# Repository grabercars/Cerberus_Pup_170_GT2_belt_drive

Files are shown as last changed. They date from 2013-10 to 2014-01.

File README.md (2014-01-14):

Cerberus Pup
========

Derivative of the Rostock 3D delta printer - A big thanks goes out to all of the people who inspired this design. There are many. 

[cc by sa 3.0]

Cerberus Pup 170 GT2 belt drive
========

1/13/2014

Cerberus Pup 170 Gt2 is a 3D Delta Robot printer that uses GT2 toothed belts and 16 or 20t pulleys. Features include Magnetic Ball joint rods (Magballs), An aluminum hotend mounting bracket that is hinged and allows the hotend tip to function as the z_probe. Bowden tube direct drive easy-load spring tensioned lever arm extruder. 170mm print surface. 500mm tall with 175mm print height.

You will need to make a set of effector rods 215mm long tip-to-tip with 3/8" ball bearings bonded to the ends. Make your own or these are available from Steve Graber - grabercars@gmail.com.

Notes:

All machined parts required to build Cerberus Pup are now all available for purchase at http://3d.grabercars.com. They are manufactured on a CNC lathe to very tight tolerances.

VERTICAL CARRIAGE DRIVE SYSTEM:
Requires GT2 belts and 20T (or 16T) pulleys. Each upper gt2 belt idler consists of 2x 623 bearings placed side-by-side. 

VERTICAL CARRIAGES:
The Cerberus vertical carriages move up and down the extrusion towers by rolling on 3 cnc machined delrin 'V' rollers per carriage. Each roller consists of a cnc machined delrin cover with two 623 bearing pressed in. The roller rides in the T-Slot of the OpenBeam or Misumi 1515 extrusion. This makes for a very smooth and accurate linear carriage system. Dual 623 V Rollers can be purchased from 3d.grabercars.com - You can use either version of the roller, the Dual 623 WIDE V or the Dual 623 V.

BELT TENSION SYSTEM:
The belts are open loop and are tensioned as they are inserted into the teeth of the Vertical Carriage Bearing Bracket. 

Cerberus Pup 170 is a very quiet printer which can be made even more quiet by use of the Astrosyn NEMA 17 vibration dampers. You will need to print 3x "Lower Outer Bracket-astrosyn_damper.stl" file instead of 3x "Lower Outer Bracket.stl" file.

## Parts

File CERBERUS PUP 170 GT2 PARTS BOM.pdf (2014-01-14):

## CERBERUS PUP 170 PRINTED PARTS BOM

CHK | QTY | FILE NAME | DESCRIPTION
| 3 | Lower Outer Bracket.stl
| 3 | Upper Outer Bracket.stl
| 3 | Vertical Carriage Bearing Bracket.stl
| 3 | Base Standoff.stl
| 1 | Effector End Platform.stl
| 1 | Extruder Lever Arm.stl
| 1 | Extruder Motor Base.stl
| 2 | VIKI Hanging Clip.stl | Optional - Bolts onto VIKI
| 2 | VIKI Hanging Base.stl | Optional - Bolts onto printer

## CERBERUS PUP 170 MISC PARTS BOM

CHK | QTY | PART NAME | DESCRIPTION
| 3 | Aluminum Carriage.dxf | Vertical Carriage
| 1 | Aluminum Base Plate.dxf | Triangular plate with holes for mounting controller
| 1 | Aluminum Bottom Fan Bar.dxf | Bottom bar with holes for cooling fan
| 1 | Aluminum Bottom Button Bar.dxf | Bottom bar with hole for power button
| 1 | Aluminum Bottom Extruder Bar.dxf | Bottom bar with holes for extruder motor
| 3 | Aluminum Top Bar.dxf | Top cross bars
| 1 | Aluminum Probe Hinge Bracket - Hotend.dxf | Slotted bracket for holding hotend
| 1 | Aluminum Push-fit Bracket - Hotend.dxf | Threaded plate for push-fit connector
| 3 | Misumi 1515 Aluminum Extrusion | Vertical bar for carriage slide
| 1 | 170mm Borosilicate Disc | Printing surface
| 6 | C.F. Effector Rod | Carbon fiber arms
| 12 | 3/8” machined ball | Bonded to C.F effector rods
| 12 | 3/8 x 3/8 Cylindrical Neodymium Magnet
| 3 | 1 meter GT2 Timing Belt
| 3 | 20-tooth GT2 Pulley | Belt drive pulleys
| 6 | Pulley Grub Screw | Fastens pulley onto stepper motor
| 4 | 3mm ID round nylon spacers | Standoff spacers for mounting the controller board
| 9 | Grabercars Dual 623 V rollers
| 6 | 623ZZ bearings | Two each side by side as upper idler pulley
| 3 | P-clips – 1/4” | Wire management clips
| 1 | 1.8mm ID Teflon Tubing | Bowden tube
| 2 | Pneumatic Push-fit Insert | Bowden tube anchors
| 1 | 0.080” Steel Rod x 50mm | Bed level probe hinge

## CERBERUS PUP 170 ELECTRONIC PARTS BOM

CHK | QTY | PART NAME | DESCRIPTION
| 1 | Panucatt Azteeg X1 Control Board
| 4 | Panucatt SureStepr SD8825 Stepper Driver | 1/32nd microstepping driver
| 1 | Panucatt MC170 Hex Heated Bed | Optional heated platform
| 1 | Panucatt VIKI LCD Control Panel | Optional LCD control panel
| 1 | 203W Xbox 360 Power Supply | Printer power supply
| 1 | Xbox 360 to Xbox Slim Adaptor
| 1 | 1.75mm Hotend | Hotend, heater resistor, and thermistor
| 4 | NEMA 17 Stepper Motor
| 4 | Micro Knife Switch | Printer endstop and bed leveling probe
| 1 | 40mm Fan | Electronics Cooling
| 1 | 20mm Fan | Hotend Cooling

## CERBERUS PUP 170 FASTENERS BOM

CHK | QTY | PART | USE/DESCRIPTION
| 2 | M5x16
| 22 | M5x12
| 24 | M5 Washer
3 | M4x14
1 | M3x30
18 | M3x25
8 | M3x16
47 | M3x12
4 | M3x8
73 | M3 Washer
30 | M3 Nut
15 | M3 Nyloc
2 | M2x12
6 | M2x10
6 | M2 Washer
2 | M2 Nut

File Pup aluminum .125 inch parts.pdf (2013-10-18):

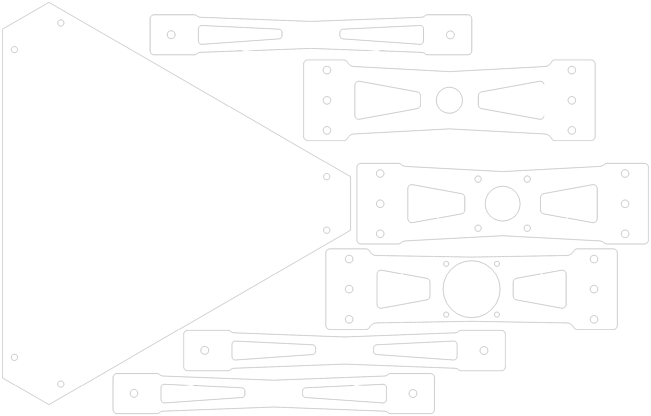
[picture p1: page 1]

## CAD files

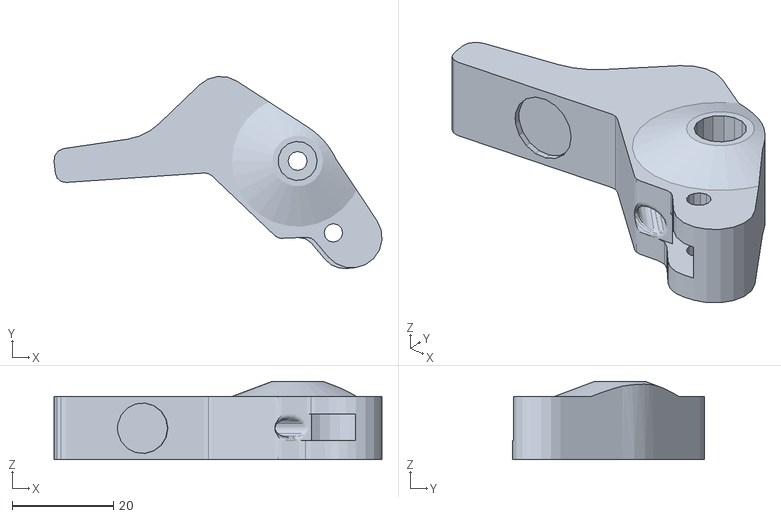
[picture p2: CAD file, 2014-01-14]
Extruder Lever Arm.stl
64.9 x 38.0 x 15.5

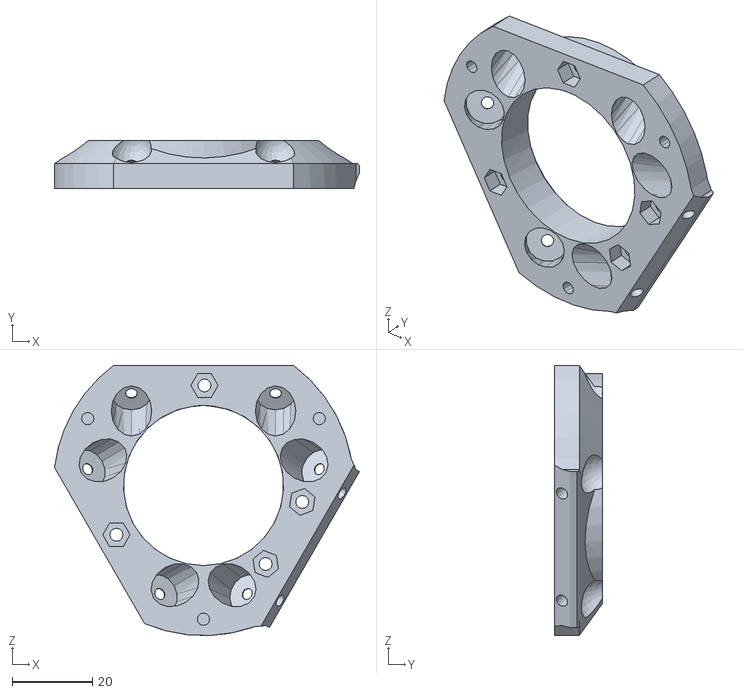
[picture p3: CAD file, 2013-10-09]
original_probe/platform_v3 - Deep Magball_original probe.stl
76.2 x 12.0 x 67.5

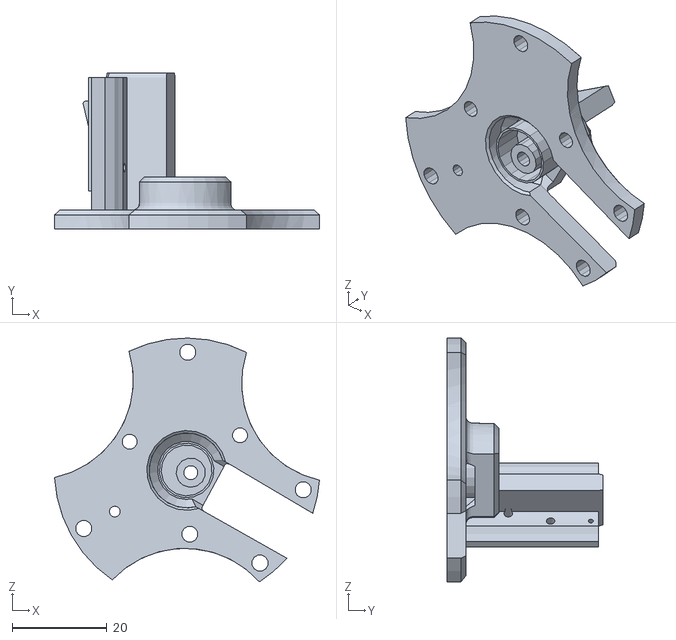
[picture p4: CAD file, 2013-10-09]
original_probe/JSlotplate_original probe.stl
56.1 x 33.1 x 51.6

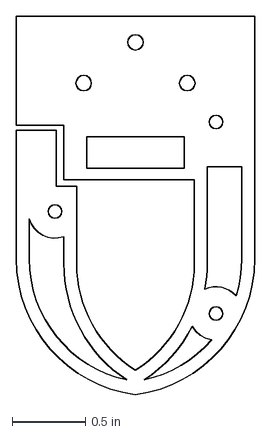
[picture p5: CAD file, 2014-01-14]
Pup vert carriage-T-6061x.125.dxf
1.63 x 2.59 in

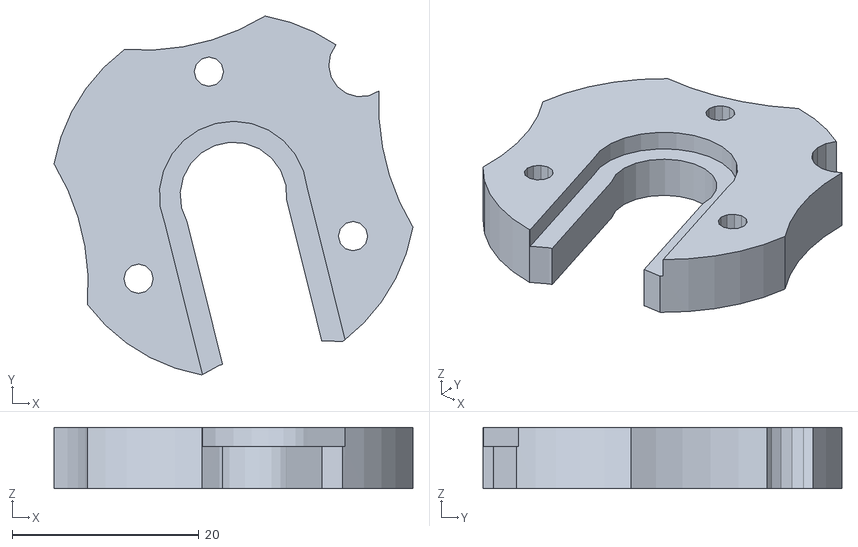
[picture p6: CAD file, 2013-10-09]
original_probe/J-slot Insert for Magball platform_original probe.stl
38.4 x 38.4 x 6.56

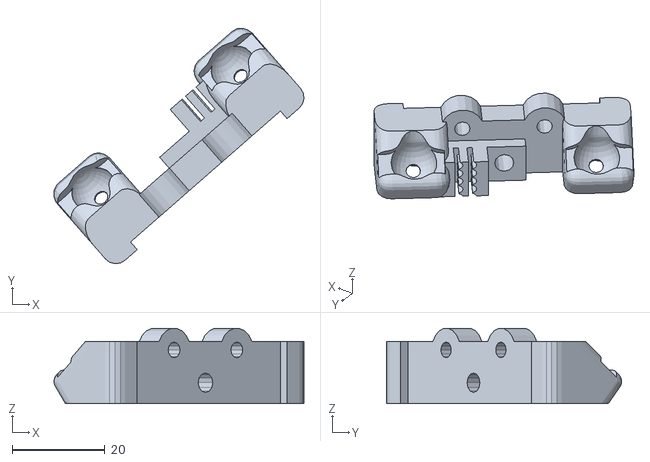
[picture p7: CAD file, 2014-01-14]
Vertical Carriage Bearing Bracket.stl
54.0 x 50.9 x 16.2

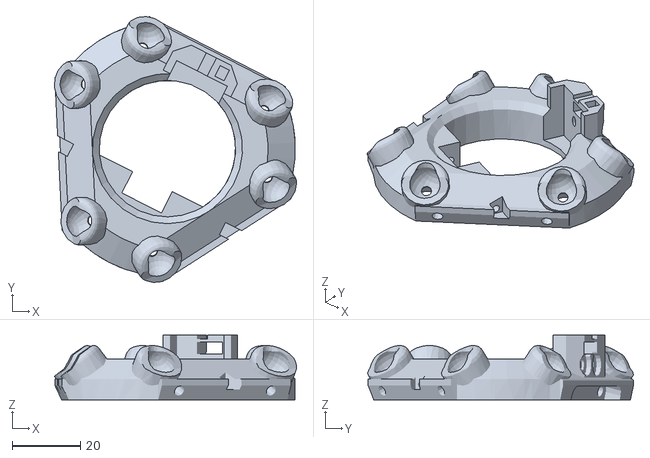
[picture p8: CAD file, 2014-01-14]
Effector End Platform.stl
71.0 x 78.0 x 19.0

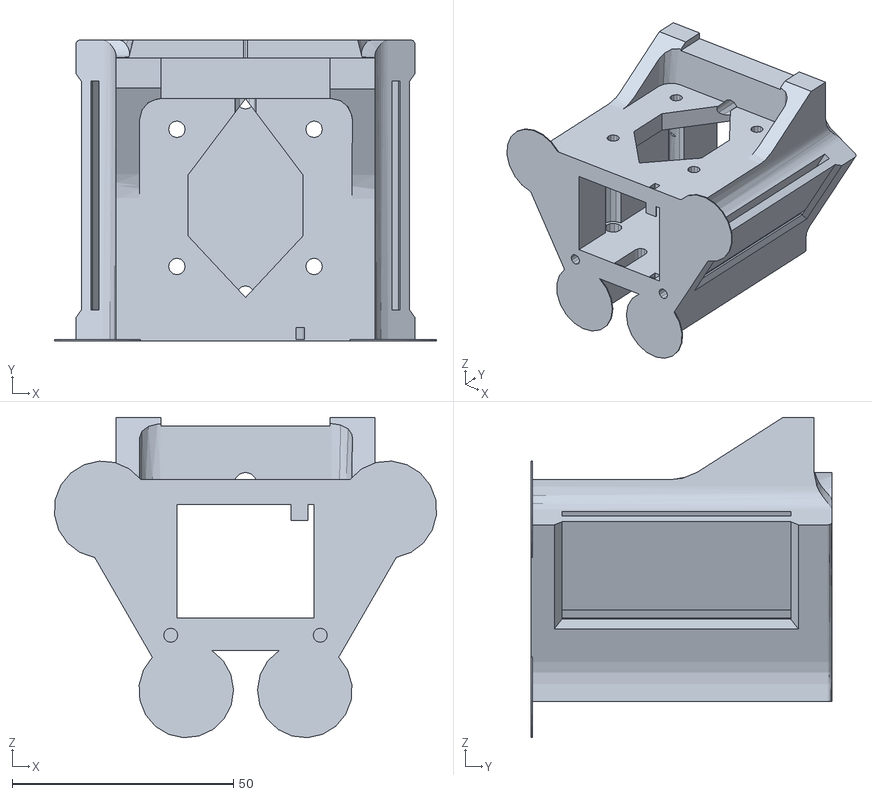
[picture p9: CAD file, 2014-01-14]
Lower Outer Bracket.stl
86.3 x 68.0 x 72.4

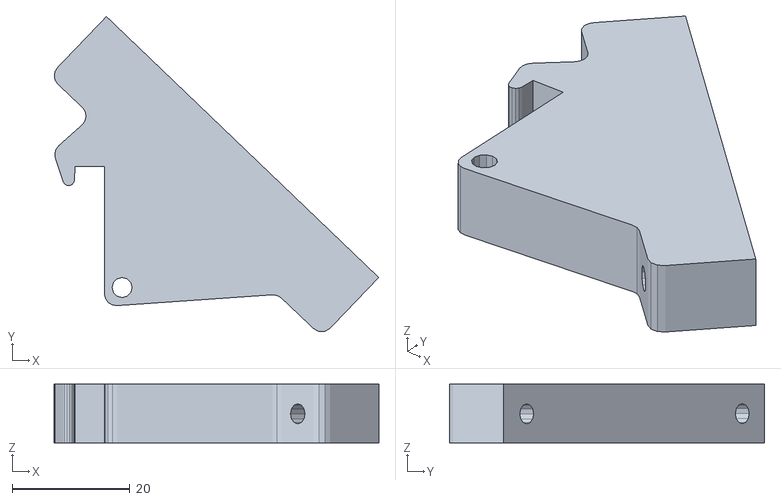
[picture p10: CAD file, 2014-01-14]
Viki Hanging Clip.stl
55.1 x 53.4 x 10.0

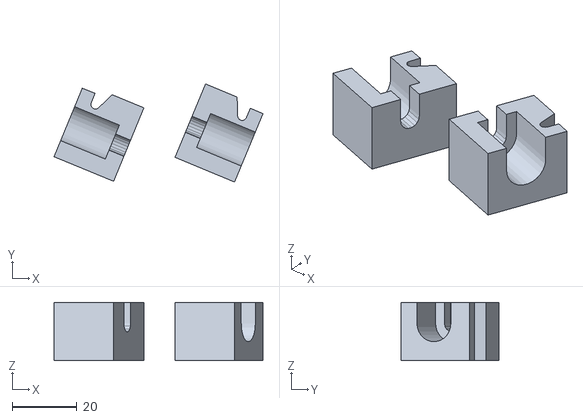
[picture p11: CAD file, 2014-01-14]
Viki Hanging Base - Pair.stl
64.8 x 30.4 x 18.0

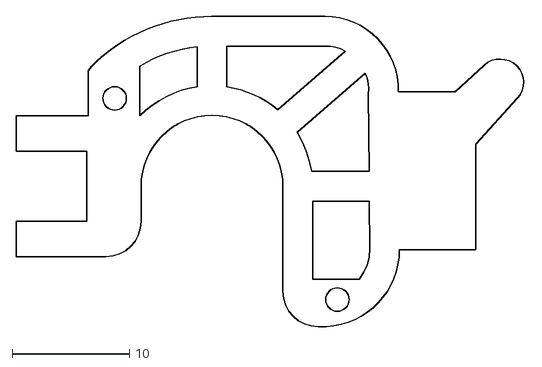
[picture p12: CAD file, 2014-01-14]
J-Hot_Single_Mount-Hinged-Alu5052.dxf
43.5 x 26.5

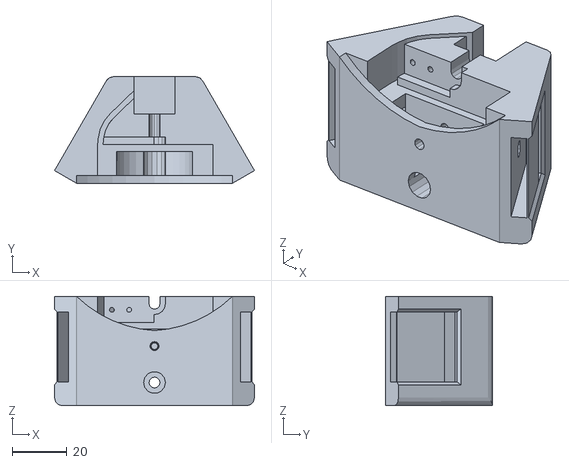
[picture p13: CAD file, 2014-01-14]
Upper Outer Bracket.stl
73.3 x 39.1 x 40.0

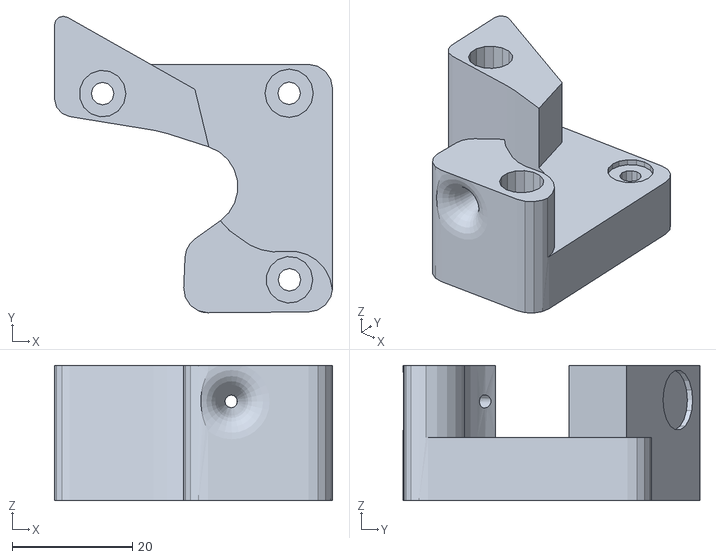
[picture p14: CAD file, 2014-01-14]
Extruder Motor Base.stl
46.2 x 49.3 x 22.5

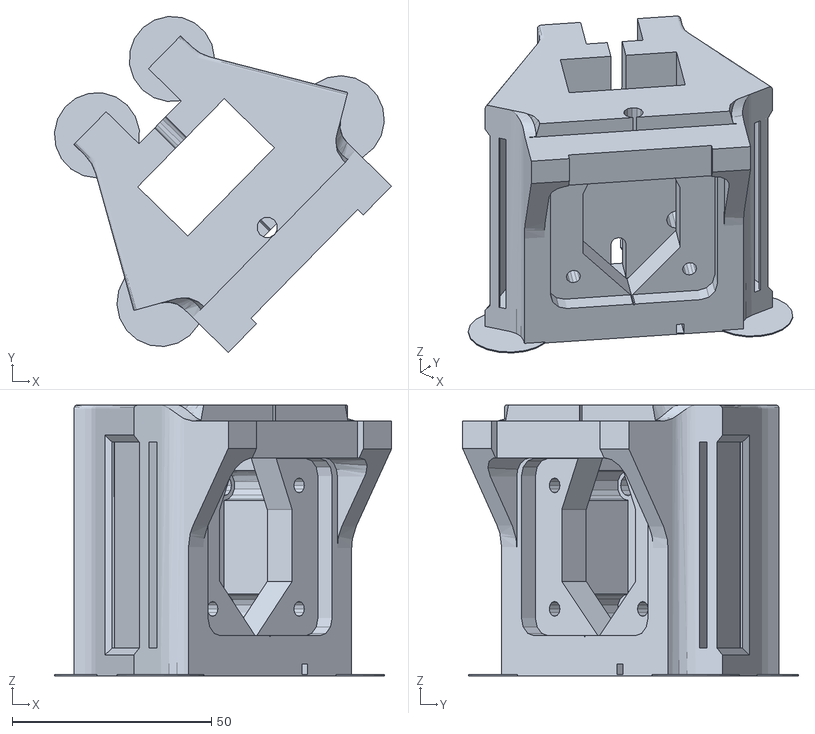
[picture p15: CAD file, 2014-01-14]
Lower Outer Bracket-astrosyn_damper.stl
84.6 x 84.3 x 68.0

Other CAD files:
Pup aluminum T-6061 .125 inch parts.dxf
Dual 623 V Roller.igs
WasteBasket_U_bracket.stl
VIKI LCD Bezel.stl
Base Standoff.stl
Fan Bracket 40 to 30 adapter.stl
HE Mount - Plastic.stl
HE Top Plate - Plastic.stl
Older files/1x Pup Platform v4 and 3x magball holders 40mm spacing - for aluminum vert carriage.STL
Older files/Fan Shroud - Magball - 40mm fan (optional).stl
Older files/HE Top Plate for platform_v3 - Magball-Hinged 2.STL
Older files/Linear Rail-Style Magball Carriage Bracket - 40mm spacing - Angled head.STL
Older files/Upper Outer Support Bracket GT2 Belt 8mm Idler.stl
Older files/platform_v3 - Magball-Hinged.stl
Older files/spiral vert carriage-OpenBeam GT2-single_grip.stl
WasteBasket.stl

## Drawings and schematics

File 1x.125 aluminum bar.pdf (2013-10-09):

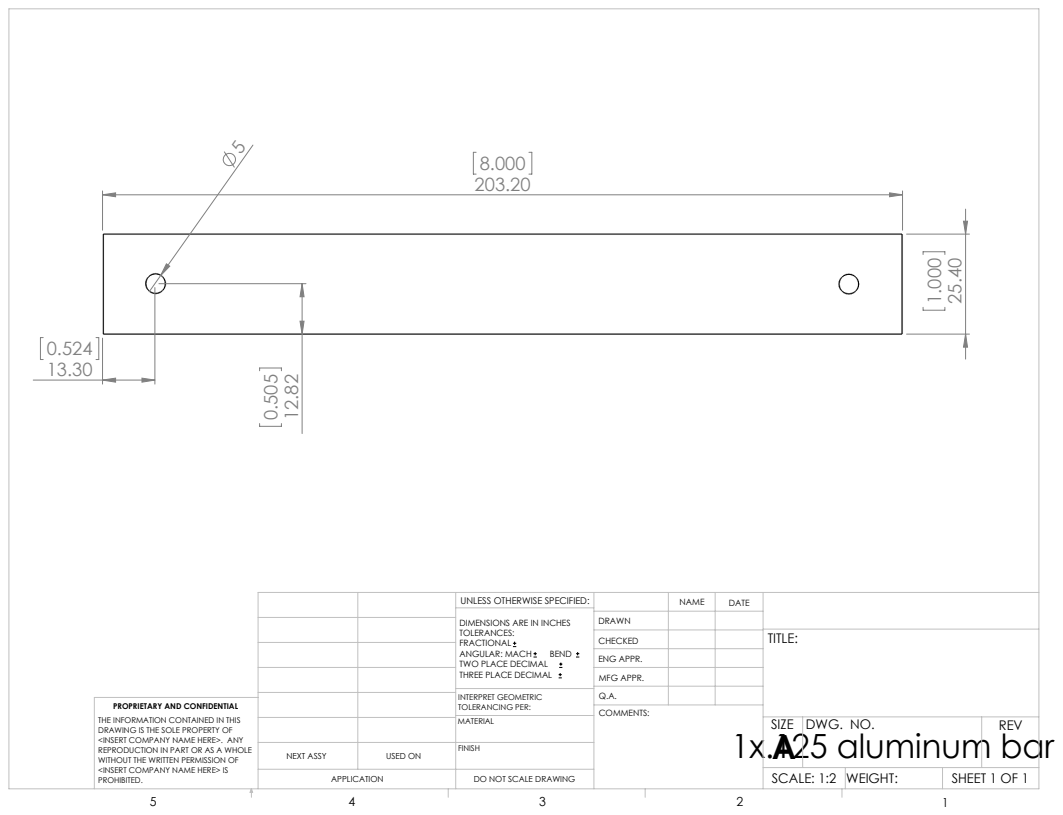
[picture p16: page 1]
1x.125 aluminum bar; SHEET 1 OF 1; SCALE: 1:2 WEIGHT:; DWG. NO.; REV; MFG APPR.; ENG APPR.; INTERPRET GEOMETRIC TOLERANCING PER:; ANGULAR: MACH; BEND; NEXT ASSY; USED ON

UNLESS OTHERWISE SPECIFIED:

DIMENSIONS ARE IN INCHES
TOLERANCES:
FRACTIONAL
TWO PLACE DECIMAL
THREE PLACE DECIMAL

PROPRIETARY AND CONFIDENTIAL
THE INFORMATION CONTAINED IN THIS
DRAWING IS THE SOLE PROPERTY OF
<INSERT COMPANY NAME HERE>. ANY
REPRODUCTION IN PART OR AS A WHOLE
WITHOUT THE WRITTEN PERMISSION OF
<INSERT COMPANY NAME HERE> IS
PROHIBITED.

DO NOT SCALE DRAWING

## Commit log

2013-10-09 Initial commit for Pup 170 GT2 belt drive
    All the files required to build a Pup 170 with GT2 belt drive. BOM and
    some other files are outdated and will be corrected in due time. Please
    take care when using the BOM.
    [Bottom Plate Standoff Bracket.stl, Dual 623 V Roller.igs, Extruder_Lever.stl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]
2013-10-18 Aluminum flat parts and new upper idler
    DXF and PDF files for water-jet cut aluminum parts. Cut from .125"
    thickness 5052 or 6061 alloy
    A change to the upper outer support bracket to make it work with two 623
    bearings as the upper idler
    [Pup aluminum .125 inch parts.dxf, Upper Outer Support Bracket GT2 Belt 3mm Idler.stl]
2013-10-18 Added a style of support for upper and lower outer brackets
    Added my own easy-to-remove support for upper and lower outer brackets.
    Now print with 0 support and at minimum 33% infill. Recommend 50%
    infill.
    [Lower Outer Support Bracket.stl, Upper Outer Support Bracket GT2 Belt 3mm Idler.stl]
2014-01-14 Revamp of the Cerberus Pup 170 GT2 Deltabot. Virtually every part has been modified and improved.
    [Base Standoff.stl, Effector End Platform.stl, Extruder Lever Arm.stl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]
2014-01-14 Full revamp of Cerberus Pup 170 GT2 Deltabot with many changes and improvements throughout.
    [1x Pup Platform v4 and 3x magball holders 40mm spacing - for aluminum vert carriage.STL, Fan Shroud - Magball - 40mm fan (optional).stl, HE Top Plate for platf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]
